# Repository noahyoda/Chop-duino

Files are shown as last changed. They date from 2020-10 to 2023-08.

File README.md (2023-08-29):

# Chopduino

### Author(s): Noah Jaussi

STEM Capstone Project

### Abstract

The goal of this experiment is to design and build a device that can electronically control a pair of chopsticks with the right precision to be used by people, who have disabilities that prevents them from using chopsticks to feed themselves. This project went through several design iterations before the final design was decided upon. Using an arduino pro micro, 18650 battery cell, an analog switch, the arduino IDE, windows 3d builder, a soldering iron, and a 3d printer to manufacture and assemble the necessary components, this project was able to make use of Science, Technology, Engineering, and Math (STEM). The process of designing and troubleshooting would not have been possible if it wasn’t for the research done beforehand, especially in the field of arduino wiring and programming. The process of prototyping this device followed the process of  testing all of the electronics on a breadboard, soldering them together, programming the arduino to function properly, modeling the base structure, 3d printing the necessary components, and assembling the frame and the electronics into their final form to be trialed for functionality improvements. There were many challenges encountered that arose in each technical division of this project and it continues to have room for improvement in future designs, should this project be continued, in the areas of size, comfort, sound deadening, and aesthetic appeal however it did fulfill all of the engineering goals it was originally set out to accomplish.

### Introduction

 In order to create the object of this project there are several techniques, programs, and skills that need to be acquired to ensure success. First it is necessary to understand the hardware required and the essential properties/interactive capabilities of said hardware for optimal performance. This includes the physical parameters for the servo, connections of the mechanical switch and button, and the pinout/specs for the microcontroller. These devices will be required to interact with the program set to be installed on the microcontroller so as to perform the functions it is intended to complete. In order to accomplish isolated and untethered operation, a rechargeable 18650 battery cell will be included, as it’s nature allows both high current power draw for the servo and consistent power output for the raw inputs on the microcontroller. Aside from the electronics, a housing will need to be constructed from 3d printed plastic which has to be confirmed to be safe for human contact. This is especially vital in this project, due to the nature and proximity the 3d printed plastics will be to objects being consumed by users. The plastic will need to be strong enough to endure the nature of its intended use while also being flexible enough to provide smooth movements for precise control.

 The most essential part of this project is the microcontroller, which will require proper implementation of its pinout abilities and programming. The Arduino Pro Micro includes 14 digital in/out (also I/O) leads and 4 analog I/O leads. This project will require one digital lead to communicate with the servo and one analog lead to interpret the incoming information from the user. The user will interact with the project via a button switch on the side. After properly connecting the switch and servo the Arduino, the micro controller chip will need to be programmed using an Integrated Development Environment (IDE), such as the one provided at arduino.cc for the specific ATMega chip on the Arduino Pro Micro. There are many options for IDE’s, however, the arduino.cc IDE was chosen for its preferential level of documentation and development status. This IDE also includes firmware that is needed to ensure that the ATMega chip in the Arduino is programmed without any issues and will utilize proper functionality. Detailed information and more on these subjects were found at Arduino.cc and the Make: Getting Started with Arduino book (Source 1).

 Programming this Arduino microcontroller will require not only hardware documentation but an understanding of simple C++ programming knowledge, as is dictated by the IDE. This is necessary as the complex nature of the task, in terms of electronics, is not something that can be easily performed without a microcontroller. The arduino will need to communicate user input from the switch to the servo in a way that translates on/off into a degree or number of rotations that the servo needs (Source 3). These translations of electrical signals will be interpreted and sent out through the program given to the arduino microcontroller.

 In order to power the Arduino and its necessary accessories, an 18650 lithium ion battery cell will be included with a voltage and current regulator to ensure proper power distribution is delivered to the electronics. This amplification and control will occur on the arduino board. It will also limit the amperage in order to protect the sensitive electronics from the high power draw of the servo motor. The 18650 battery cells are lithium ion, which means that the battery in this project will need to have overcharge/discharge protection circuits. This is necessary, not only to ensure battery life, but also to prevent the battery from becoming a fire hazard. According to previous research and the properties of power distribution in arduinos, these concerns will not manifest should the project be assembled exactly according to its design guidelines (Source 2).

 To make the prototyping and development of this project faster, a 3d printer will be used to make the frame and housing for the electronics as well as other necessary items. Having plastics that are toxic to humans and not rigid enough to support the required components are important design concerns to be considered for this project. Fortunately, these concerns has been tested before and it has been found that consumer grade Acrylonitrile butadiene styrene (ABS) and Thermoplastic Polyurethane (TPU) plastic filament are both not toxic to humans (unless burned and fumes are inhaled, see source 5) and provide the mixture of strength and flexibility required for this projects success (source 4). There are many other plastics that could be used but considering this project’s proximity to food that will be consumed, ABS and TPU plastics were decided upon as the final developing material for this project.

### Materials and Procedures

Materials:

-   Computer to run Windows 3d builder    
-   3d printer (creality ender 3)
-   ABS + TPU 3d printer filament
-   18650 battery
-   Arduino pro micro
-   Analog switch    
-   Breadboard    
-   Wire clips    
-   Chopsticks    
-   Soldering iron + solder   
-   Wires    
-   Small tension spring
-   9g servo    

### Procedure:

1.  Prototype electronics circuit on breadboard
2.  Revise until all connections are functional
3.  Design code for arduino
4.  Upload and test code in arduino
5.  Revise code until proper functionality
6.  Open 3d builder and design first 3d printable prototype
7.  Save 3d model in cura printing software
8.  Upload model to 3d printer
9.  Solder electronics together while model is 3d printing
10.  Assemble 3d model and observe potential changes
11.  Return to 3d builder to add changes to the 3d model
12.  Begin print of revised model
13.  Repeat assemble, observation, edit, and 3d print until fully functional design is achieved
  
### Data Analysis

Figure A: Prototype v.1





Figure B: Prototype v.1.2





FIgure C: Prototype v.2





Electronics v.1



Electronics Diagram



Engineering Challenges

Observations

1
-   Initially the electronics were assembled and tested which proved trials as the analog pin  for the switch was giving off unusual pulses making the servo uncontrollable. This was fixed with an analogWrite(_,0); statement to reset the analog signal on pin A0 to zero after every run of the program.
    
2

-   While testing the electronics the first servo broke and would spin out of control so several more servos were tested until a 180* servo worked with full control.

3
-   When assembling the 3d printed frame the plastic had to be welded together using a soldering iron which was a challenge and required the use of multiple prints to get successful and strong bonds.
    
4
-   The servo placement on the printed frame required multiple trials before it could provide the proper tension on the spring to pull the pivoting chopstick into place and push it back when finished with its cycle. To solve this the servo was placed on the bottom of the overall device.
    
5
-   The final challenge before the working product was chopstick alignment. The moving chopstick had the challenge of shifting the still chopstick far enough out of place that it proved not functional. This was resolved by welding a plastic brace over the still chopstick.
    
6
-   There was difficulty getting an ir distance sensor to ship to Hawaii so a model function change was altered to use a button for activation of the software devices in place of the distance sensor as originally planned.

### Conclusion

This project is based on the idea that STEM can create a device that provides functionality to those in need of assistive eating devices. The result of this idea was an electronically controlled, self-contained device that can close, hold closed, and open a pair of chopsticks under the control of a single button. This device encountered many challenges as prototypes were developed that had to be overcome in many unique ways that incorporated all fields of STEM.

  In chronological order of development, the first engineering challenge encountered was found in the connections between the switch/button and servo to the ATMega chip controlling the Arduino pro micro. The pins were either being shared with other logic data lines on the Arduino or there was interference that would cause the electrical values of the pins to vary from 0 to 1000 (state of all off to all on). This complication would cause the button to not be recognized while being pushed and the servo to twitch and not respond at times. The troubleshooting process for this problem required analysis into the electrical engineering of the Arduino pro micro to find the problem and then was resolved in the technological field through extra lines to the code. By adding analog write functions to reset the button pin value every time the program is run, the Arduino verified the switch position value. This switch problem was resolved by using the digital write function. The servo was able to reassign the pin value to the servo rotational status in a way to keep it in the proper orientation and clear the interference that the connection was experiencing. During the process of troubleshooting these issues, the first servo burnt out and had to be replaced. The next issue was found in the code, which would not reset the servo position at times and not react to user input through the button on other occasions. This was found, in the troubleshooting process, to be the fault of using an if-else statement to run the servo. To remedy this issue, more technical aspects were applied through a double “if” statement, which was used to run individual loops for the function of opening and closing the servo direction. Following this, the 3d model was designed and printed for the housing of the project, which went through several designs before being functional. The first design had an error in which the gear sockets were printed too far apart to prevent the gears from interacting. This was fixed by bringing the gears 5mm closer to each other. After fixing that, it was found that the design did not have enough room for the electronics needed and more importantly could not provide the servo with a position to get enough leverage to move the chopsticks into open and closed positions. Eventually, the model was scrapped and a new model was designed based on the flexibility of the 3d printed plastic rather than a gear system that solved the electronic housing and servo positioning issues but required more plastic welding to be assembled.

  Having built a functioning project that completes the engineering requirements set at the beginning of this project, there are several things that could be done differently or better upon repeating this project. The project would greatly benefit from precise measurements with better software to require less post-processing in the assembly. Additionally, adding rails to guide the chopsticks and downsizing the flexible joint for the chopsticks would improve performance. More time could be spent making a better grip for the model would improve the comfort of the device. As far as electronics are concerned, a custom circuit board with power and grounding rails, rather than the current clips, would help with downsizing the project. In the future a single ATTiny chip could also be used to decrease size and power consumption alongside the custom PCB. The solder joints could be improved with more flux in the joints that could increase their potential longevity and efficiency. Alongside that, adding a circuit to reset the servo position before cutting the power, after hitting the power switch, would reduce manual maintenance. Silicon coating on the electronics would make them waterproof to alleviate the concern when using this device for eating near liquids. The code for this project isn’t as efficient as it could be and could use cleaning. This could also be solved by using a different chip, such as the ATTiny, which would not require a solution to fix interference. The code could also use some changes to make the servo quieter. The battery would benefit from the use of a step-up circuit to provide power at a higher voltage to the servo and decrease the motor noise.

This experiment provides a solution for individuals with disabilities, who struggle to feed themselves without assistance, by automating processes that are not within their capabilities and necessary to be independent. This device automates the coordination and strength required to precisely close and hold onto an object using chopsticks to feed themselves. By simplifying these actions to the control of a button press, people are able to focus on carrying food to their mouth without requiring the assistance that would be necessary to perform this action otherwise.

## References

Source 1

Banzi, M., & Shiloh, M. (2014). Make: Getting Started with Arduino. Maker Media, Inc. 

Source 2

Ecker, M., Nieto, N., Käbitz, S., Schmalstieg, J., Blanke, H., Warnecke, A., & Sauer, D. U. (2013, October 11). Calendar and cycle life study of Li(NiMnCo)O2-based 18650 lithium-ion batteries. Retrieved from https://www.sciencedirect.com/science/article/abs/pii/S0378775313016510.

Source 3

Minns, P. D. (2013). C programming for the Pc the Mac and the Arduino microcontroller system. Bloomington, IN: AuthorHouse.

Source 4

SajTom Light Future. (n.d.). Is 3D printing safe? Analysis of the thermal treatment of thermoplastics: ABS, PLA, PET, and nylon. Retrieved from https://www.tandfonline.com/doi/abs/10.1080/15459624.2017.1285489.

Source 5

nnn946@gmail.com. “TPU Filament 3D Printing Material – The Complete Guide (Mar. 2020).” AllThat3D, AllThat3D, 25 Oct. 2019, www.allthat3d.com/tpu-filament/. 

Source 6

Warren, J.-D., Adams, J., & Molle, H. (1970, January 1). Arduino for Robotics. Retrieved from [https://link.springer.com/chapter/10.1007/978-1-4302-3184-4_2](https://link.springer.com/chapter/10.1007/978-1-4302-3184-4_2).

Source 7

My Continuous Rotation Servo Won't Stop Spinning?, 27 Feb. 2015, forum.arduino.cc/index.php?topic=304146.0.

Source 8

“How to Make My Servo Stop Twitching.” How to Make a Servo Stop Twitching, 26 June 2018, forum.arduino.cc/index.php?topic=555150.0.

Source 9

“Language Reference.” Arduino Reference, www.arduino.cc/reference/en/.

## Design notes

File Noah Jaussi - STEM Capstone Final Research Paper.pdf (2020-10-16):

# Chopduino

## Noah Jaussi - Kahuku High School

## STEM Capstone Project

# Abstract

The goal of this experiment is to design and build a device that can electronically control a pair of chopsticks with the right precision to be used by people, who have disabilities that prevents them from using chopsticks to feed themselves. This project went through several design iterations before the final design was decided upon. Using an arduino pro micro, 18650 battery cell, an analog switch, the arduino IDE, windows 3d builder, a soldering iron, and a 3d printer to manufacture and assemble the necessary components, this project was able to make use of Science, Technology, Engineering, and Math (STEM). The process of designing and troubleshooting would not have been possible if it wasn’t for the research done beforehand, especially in the field of arduino wiring and programming. The process of prototyping this device followed the process of testing all of the electronics on a breadboard, soldering them together, programming the arduino to function properly, modeling the base structure, 3d printing the necessary components, and assembling the frame and the electronics into their final form to be trialed for functionality improvements. There were many challenges encountered that arose in each technical division of this project and it continues to have room for improvement in future designs, should this project be continued, in the areas of size, comfort, sound deadening, and aesthetic appeal however it did fulfill all of the engineering goals it was originally set out to accomplish.

# Introduction

In order to create the object of this project there are several techniques, programs, and skills that need to be acquired to ensure success. First it is necessary to understand the hardware required and the essential properties/interactive capabilities of said hardware for optimal performance. This includes the physical parameters for the servo, connections of the mechanical switch and button, and the pinout/specs for the microcontroller. These devices will be required to interact with the program set to be installed on the microcontroller so as to perform the functions it is intended to complete. In order to accomplish isolated and untethered operation, a rechargeable 18650 battery cell will be included, as it’s nature allows both high current power draw for the servo and consistent power output for the raw inputs on the microcontroller. Aside from the electronics, a housing will need to be constructed from 3d printed plastic which has to be confirmed to be safe for human contact. This is especially vital in this project, due to the nature and proximity the 3d printed plastics will be to objects being consumed by users. The plastic will need to be strong enough to endure the nature of its intended use while also being flexible enough to provide smooth movements for precise control. The most essential part of this project is the microcontroller, which will require proper implementation of its pinout abilities and programming. The Arduino Pro Micro includes 14 digital in/out (also I/O) leads and 4 analog I/O leads. This project will require one digital lead to communicate with the servo and one analog lead to interpret the incoming information from the user. The user will interact with the project via a button switch on the side. After properly connecting the switch and servo the Arduino, the micro controller chip will need to be programmed using an Integrated Development Environment (IDE), such as the one provided at arduino.cc for the specific ATMega chip on the Arduino Pro Micro. There are many options for IDE’s, however, the arduino.cc IDE was chosen for its preferential level of documentation and development status. This IDE also includes firmware that is needed to ensure that the ATMega chip in the Arduino is programmed without any issues and will utilize proper functionality. Detailed information and more on these subjects were found at Arduino.cc and the Make: Getting Started with Arduino book (Source 1).
Programming this Arduino microcontroller will require not only hardware documentation but an understanding of simple C++ programming knowledge, as is dictated by the IDE. This is necessary as the complex nature of the task, in terms of electronics, is not something that can be easily performed without a microcontroller. The arduino will need to communicate user input from the switch to the servo in a way that translates on/off into a degree or number of rotations that the servo needs (Source 3). These translations of electrical signals will be interpreted and sent out through the program given to the arduino microcontroller.
In order to power the Arduino and its necessary accessories, an 18650 lithium ion battery cell will be included with a voltage and current regulator to ensure proper power distribution is delivered to the electronics. This amplification and control will occur on the arduino board. It will also limit the amperage in order to protect the sensitive electronics from the high power draw of the servo motor. The 18650 battery cells are lithium ion, which means that the battery in this project will need to have overcharge/discharge protection circuits. This is necessary, not only to ensure battery life, but also to prevent the battery from becoming a fire hazard. According to previous research and the properties of power distribution in arduinos, these concerns will not manifest should the project be assembled exactly according to its design guidelines (Source 2). To make the prototyping and development of this project faster, a 3d printer will be used to make the frame and housing for the electronics as well as other necessary items. Having plastics that are toxic to humans and not rigid enough to support the required components are important design concerns to be considered for this project. Fortunately, these concerns has been tested before and it has been found that consumer grade Acrylonitrile butadiene styrene (ABS) and Thermoplastic Polyurethane (TPU) plastic filament are both not toxic to humans (unless burned and fumes are inhaled, see source 5) and provide the mixture of strength and flexibility required for this projects success (source 4). There are many other plastics that could be used but considering this project’s proximity to food that will be consumed, ABS and TPU plastics were decided upon as the final developing material for this project.

# Materials and Procedures

Materials:
- Computer to run Windows 3d builder
- 3d printer (creality ender 3)
- ABS + TPU 3d printer filament

- 18650 battery
- Arduino pro micro
- Analog switch
- Breadboard
- Wire clips
- Chopsticks
- Soldering iron + solder
- Wires
- Small tension spring
- 9g servo

Procedure:
1. Prototype electronics circuit on breadboard
2. Revise until all connections are functional
3. Design code for arduino
4. Upload and test code in arduino
5. Revise code until proper functionality
6. Open 3d builder and design first 3d printable prototype
7. Save 3d model in cura printing software
8. Upload model to 3d printer
9. Solder electronics together while model is 3d printing 10.Assemble 3d model and observe potential changes
11.Return to 3d builder to add changes to the 3d model
12.Begin print of revised model
13.Repeat assemble, observation, edit, and 3d print until fully functional design is achieved

# Data Analysis

Figure A: Prototype v.1

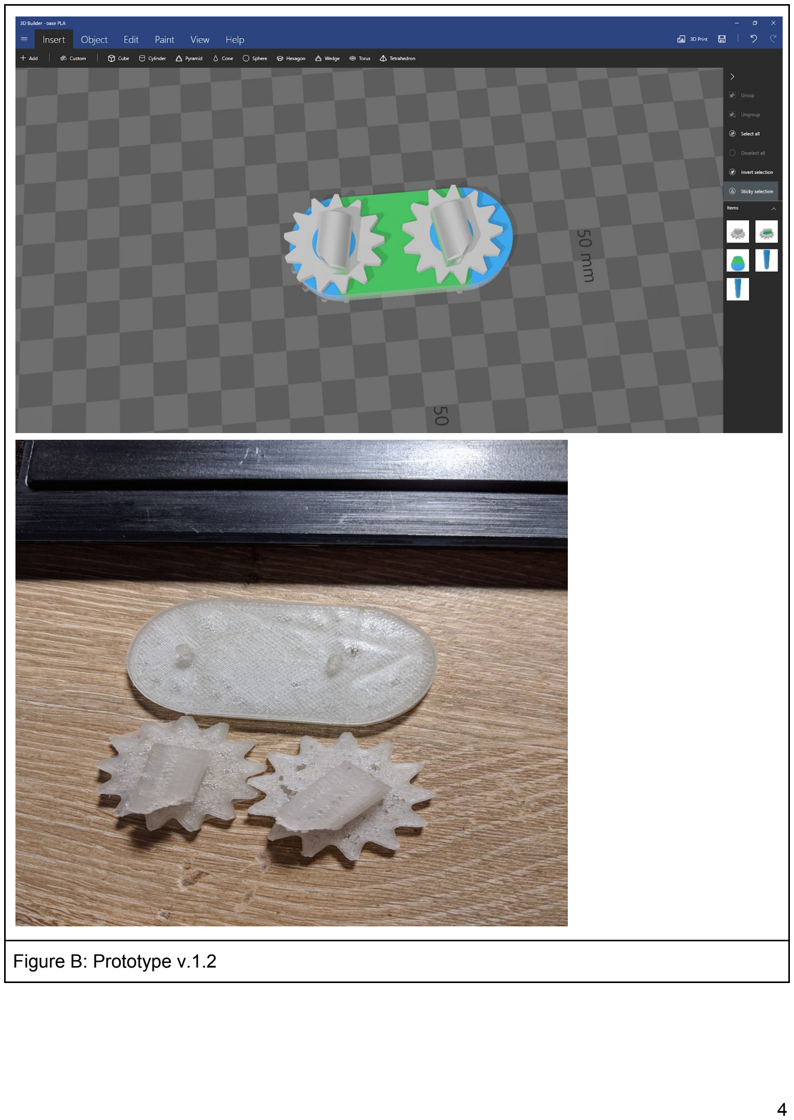
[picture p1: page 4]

Figure B: Prototype v.1.2

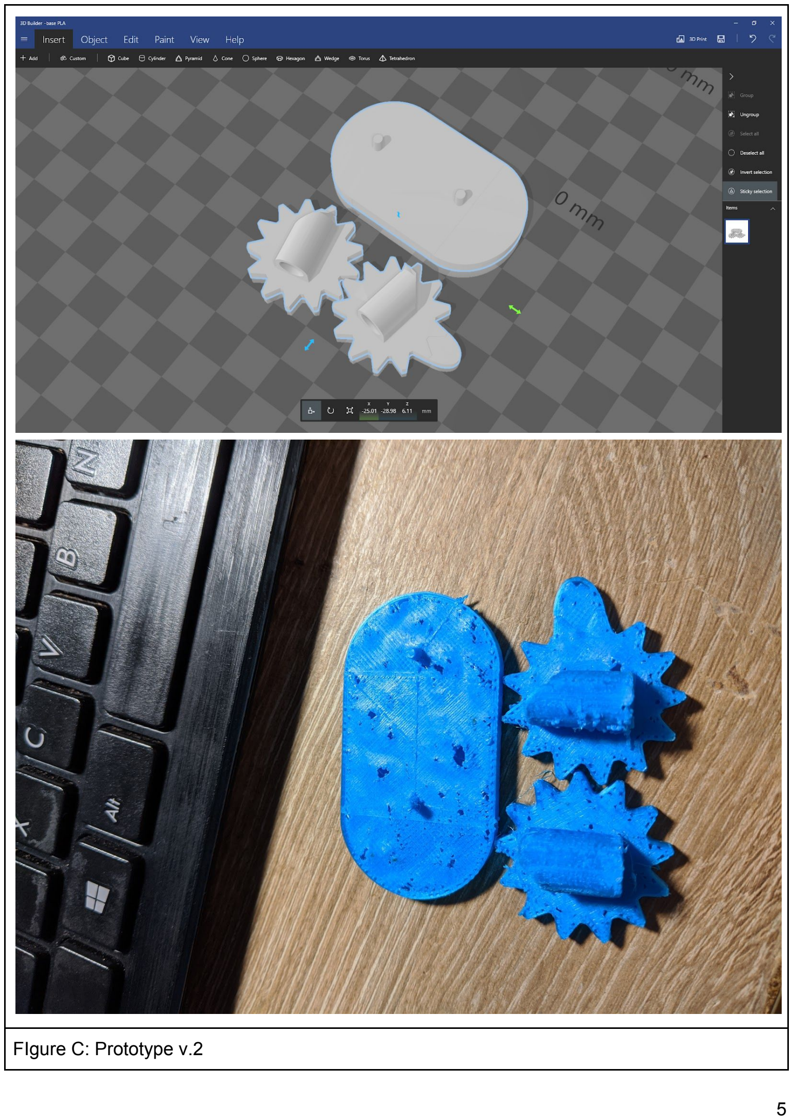
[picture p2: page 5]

FIg

u

r

e

C: P

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
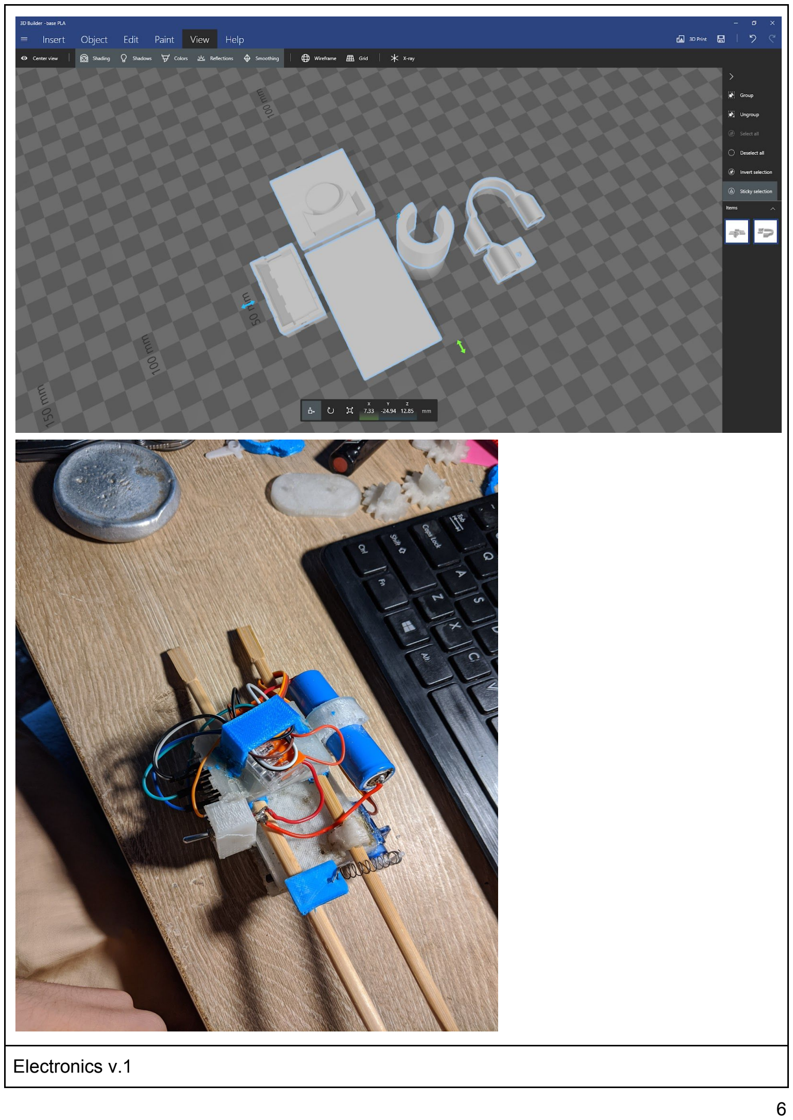
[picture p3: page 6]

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
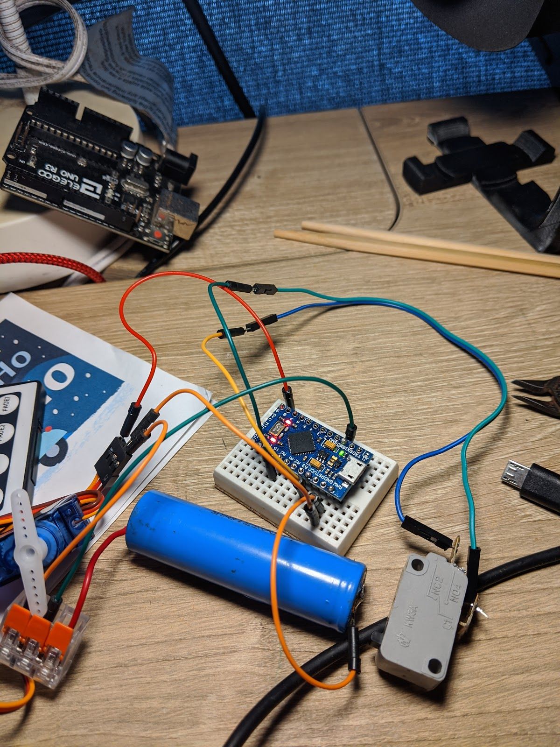
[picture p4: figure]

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
rv; int switchA

=

A

0; int val = 0; void setup() { // put setup code

h

e

r

e
s

e

rv.a

t

t

a

c

h

(

9

); serv.write(0); delay(100); val = analogRe

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
); //pinMode(15, INPUT); }void loop() { // put your main code here

if(val > 1000){
//serv.attach(9);
while(val > 1000){
serv.write(90);
}
} else {
//serv.attach(9);
serv.write(0);
//serv.detach();

delay(300);
}
}

Code v.2

#include <Servo.h>

Servo myservo; // create servo object to control a servo

int pos = 0; // variable to store the servo position int button = 4; // The button will be on Pin 4
int val = 0;
int switchA = A0;

void setup(){
myservo.attach(9); // attaches the servo on pin 9 to the servo object pinMode(pos, OUTPUT);
pinMode(button, INPUT);
digitalWrite (button, LOW);
Serial.begin(9600);
}

void loop(){
Serial.println(val);
val = analogRead(switchA);
if (val > 1000)
for(pos = 0; pos < 90; pos += 90){ // goes from 0 degrees to 90 degrees
myservo.write(pos); | // tell servo to go to position in variable 'pos'
delay(30); | // waits for the servo to reach the position
}
if (val < 1000)
for(pos = 90; pos>=90; pos-=90){ // goes from 90 degrees to 0 degrees
myservo.write(pos); | // tell servo to go to position in variable 'pos'
delay(100); | // waits for the servo to reach the position
analogWrite(val, 0);

}
}

Electronics Diagram

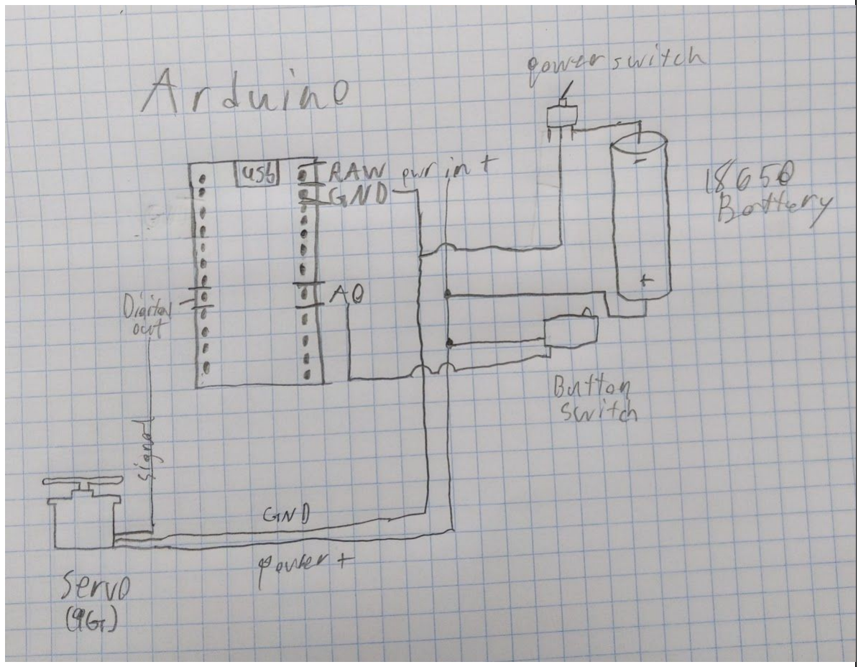
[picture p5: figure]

Engineerin g Challenges | Observations
1 | ● Initially the electronics were assembled and tested which proved trials as the analog pin for the switch was giving off unusual pulses making the servo uncontrollable. This was fixed with an analogWrite(_,0); statement to reset the analog signal on pin A0 to zero after every run of the program.
2 | ● While testing the electronics the first servo broke and would spin out of

| control so several more servos were tested until a 180* servo worked with full control.
3 | ● When assembling the 3d printed frame the plastic had to be welded together using a soldering iron which was a challenge and required the use of multiple prints to get successful and strong bonds.
4 | ● The servo placement on the printed frame required multiple trials before it could provide the proper tension on the spring to pull the pivoting chopstick into place and push it back when finished with its cycle. To solve this the servo was placed on the bottom of the overall device.
5 | ● The final challenge before the working product was chopstick alignment. The moving chopstick had the challenge of shifting the still chopstick far enough out of place that it proved not functional. This was resolved by welding a plastic brace over the still chopstick.
6 | ● There was difficulty getting an ir distance sensor to ship to Hawaii so a model function change was altered to use a button for activation of the software devices in place of the distance sensor as originally planned.

# Conclusion

This project is based on the idea that STEM can create a device that provides functionality to those in need of assistive eating devices. The result of this idea was an electronically controlled, self-contained device that can close, hold closed, and open a pair of chopsticks under the control of a single button. This device encountered many challenges as prototypes were developed that had to be overcome in many unique ways that incorporated all fields of STEM.
In chronological order of development, the first engineering challenge encountered was found in the connections between the switch/button and servo to the ATMega chip controlling the Arduino pro micro. The pins were either being shared with other logic data lines on the Arduino or there was interference that would cause the electrical values of the pins to vary from 0 to 1000 (state of all off to all on). This complication would cause the button to not be recognized while being pushed and the servo to twitch and not respond at times. The troubleshooting process for this problem required analysis into the electrical engineering of the Arduino pro micro to find the problem and then was resolved in the technological field through extra lines to the code. By adding analog write functions to reset the button pin value every time the program is run, the Arduino verified the switch position value. This switch problem was resolved by using the digital write function. The servo was able to reassign the pin value to the servo rotational status in a way to keep it in the proper orientation and clear the interference that the connection was experiencing. During the process of troubleshooting these issues, the first servo burnt out and had to be replaced. The next issue was found in the code, which would not reset the servo position at times and not react to user input through the button on other occasions. This was found, in the troubleshooting process, to be the fault of using an if-else statement to run the servo. To remedy this issue, more technical aspects were applied through a double “if” statement, which was used to run individual loops for the function of opening and closing the servo direction. Following this, the 3d model was designed and printed for the housing of the project, which went through several designs before being functional. The first design had an error in which the gear sockets were printed too far apart to prevent the gears from interacting. This was fixed by bringing the gears 5mm closer to each other. After fixing that, it was found that the design did not have enough room for the electronics needed and more importantly could not provide the servo with a position to get enough leverage to move the chopsticks into open and closed positions. Eventually, the model was scrapped and a new model was designed based on the flexibility of the 3d printed plastic rather than a gear system that solved the electronic housing and servo positioning issues but required more plastic welding to be assembled.
Having built a functioning project that completes the engineering requirements set at the beginning of this project, there are several things that could be done differently or better upon repeating this project. The project would greatly benefit from precise measurements with better software to require less post-processing in the assembly. Additionally, adding rails to guide the chopsticks and downsizing the flexible joint for the chopsticks would improve performance. More time could be spent making a better grip for the model would improve the comfort of the device. As far as electronics are concerned, a custom circuit board with power and grounding rails, rather than the current clips, would help with downsizing the project. In the future a single ATTiny chip could also be used to decrease size and power consumption alongside the custom PCB. The solder joints could be improved with more flux in the joints that could increase their potential longevity and efficiency. Alongside that, adding a circuit to reset the servo position before cutting the power, after hitting the power switch, would reduce manual maintenance. Silicon coating on the electronics would make them waterproof to alleviate the concern when using this device for eating near liquids. The code for this project isn’t as efficient as it could be and could use cleaning. This could also be solved by using a different chip, such as the ATTiny, which would not require a solution to fix interference. The code could also use some changes to make the servo quieter. The battery would benefit from the use of a step-up circuit to provide power at a higher voltage to the servo and decrease the motor noise.
This experiment provides a solution for individuals with disabilities, who struggle to feed themselves without assistance, by automating processes that are not within their capabilities and necessary to be independent. This device automates the coordination and strength required to precisely close and hold onto an object using chopsticks to feed themselves. By simplifying these actions to the control of a button press, people are able to focus on carrying food to their mouth without requiring the assistance that would be necessary to perform this action otherwise.

# References

Source 1
Banzi, M., & Shiloh, M. (2014). Make: Getting Started with Arduino. Maker Media, Inc. Source 2
Ecker, M., Nieto, N., Käbitz, S., Schmalstieg, J., Blanke, H., Warnecke, A., & Sauer, D. U. (2013, October 11). Calendar and cycle life study of Li(NiMnCo)O2-based 18650 lithium-ion batteries. Retrieved from https://www.sciencedirect.com/science/article/abs/pii/S0378775313016510.
Source 3
Minns, P. D. (2013). C programming for the Pc the Mac and the Arduino microcontroller system. Bloomington, IN: AuthorHouse.
Source 4
SajTom Light Future. (n.d.). Is 3D printing safe? Analysis of the thermal treatment of thermoplastics: ABS, PLA, PET, and nylon. Retrieved from https://www.tandfonline.com/doi/abs/10.1080/15459624.2017.1285489.
Source 5
nnn946@gmail.com. “TPU Filament 3D Printing Material – The Complete Guide (Mar. 2020).” AllThat3D, AllThat3D, 25 Oct. 2019, www.allthat3d.com/tpu-filament/.
Source 6
Warren, J.-D., Adams, J., & Molle, H. (1970, January 1). Arduino for Robotics. Retrieved from https://link.springer.com/chapter/10.1007/978-1-4302-3184-4_2.
Source 7
My Continuous Rotation Servo Won't Stop Spinning?, 27 Feb. 2015, forum.arduino.cc/index.php?topic=304146.0.
Source 8
“How to Make My Servo Stop Twitching.” How to Make a Servo Stop Twitching, 26 June 2018, forum.arduino.cc/index.php?topic=555150.0.
Source 9
“Language Reference.” Arduino Reference, www.arduino.cc/reference/en/.

# Grading Rubric (DO NOT EDIT)

Grade

Teacher Rubric Settings: t10060tftc jrasmussen _

Rubric Categories | Exemplary | Meets Proficiency | Approaching Proficiency | Developing Proficiency
Content Understanding | Report reflects an overall accurate and thorough understanding of all included S, T, E, and M content and concepts. | Report reflects an overall accurate understanding of most included S, T, E, and M content and concepts. | Report reflects a limited understanding of all included S, T, E, and M content and concepts. | Report reflects a misunderstandin g or lack of included S, T, E, and M content.
Introduction and | Clearly stated, introduces the topic of the | Clearly stated, introduces the topic of the | In the introduction, the topic of the | The topic of the paper and research

Background paper and the main points to be discussed. Explains background information, presents the research problem or questions with rationale.

paper. Provides
background
information and
presents the
research
problem or
questions.

paper and the
research
problem or
questions are
stated, but need
to be clarified or
refined.

problem or
questions are
unclear or not
stated.

Materials and
Procedures

Testable
hypotheses or
predictions are
clearly
articulated.
Research design
is appropriate to
the research
problem/questio
ns. Procedures
are described in
paragraph form,
outlined
sequentially,
and adequately
detailed.

Testable
hypotheses or
predictions are
stated.
Research design
is mostly
appropriate to
the research
problem/questio
ns. Procedures
are described in
paragraph form,
sequentially,
and detailed.

Hypotheses are
not testable or
incomplete.
Research design
needs
improvement to
address the
research
problem/questio
ns. Procedures
are not
described in
paragraph form
(e.g. bulleted
list) or not
sufficiently
detailed.

No hypotheses
or predictions
are stated.
Research design
is not
appropriate to
the research
problem/questio
ns. Procedures
are not
described or
inaccurate.
Results/Data | Data are presented clearly and cleanly, in tables or graphs as appropriate. Data are labeled and titled. | Data are presented clearly, in tables or graphs as appropriate. Data are labeled and titled. | Data are presented, but are unorganized and difficult to follow. | Data are not presented or inaccurate
Data Analysis | All calculations are shown and results are correct and labeled appropriately. | Most calculations are shown and results are correct and labeled appropriately. | Some calculations are shown and results are mostly labeled appropriately. | No calculations are shown OR results are inaccurate or mislabeled.

Conclusions

Conclusions
indicate whether
the hypothesis
was supported.
Claims about
interpretation of
the data are
supported by
evidence.
Explanations or
solutions
proposed are
based on
evidence.
Sources of
experimental
error or
limitations are
presented and
their possible
effects are
discussed.
Ways to reduce
error and
limitations are
proposed.

Conclusions
indicate whether
the hypothesis
was supported,
based on data.
Explanations or
solutions
proposed are
based on
evidence.
Sources of
experimental
error or
limitations are
presented.
Ways to reduce
error and
limitations are
proposed.

Conclusions
describe what
was learned in
the experiment,
but are not
based on data.
Experimental
errors may be
mentioned, but
are not
described.

No conclusions
are presented or
are not related
to the
investigation.

Organization

Purposeful
structure helps
reader follow
writer’s thinking.
Strong
lead—conclusio
n that provides
closure.
Thoughtful
transitions
clearly connect
ideas. Design
helps reader
process
ideas—main
ideas stand out.

Organization
makes it fairly
easy to follow
discussion.
Functional lead
and conclusion.
Helpful
transitions often
suggest
connections.
Overall design
works—writer
sometimes
dwells on trivia
or skims over
complex topics.

Reader can
follow
story/discussion
if attentive. Lead
formulaic or
misleading,
conclusion
formulaic or
abrupt.
Transitions
sometimes
missing or
mechanical.
Structure may
be formulaic or
confusing—paci
ng rushed or
sluggish.

Hard to follow,
even with effort.
Lead or
conclusion
missing,
formulaic, or
misleading.
Transitions
unclear, missing,
or not helpful in
linking ideas.
Significant
reorganization
needed—pacing
feels random
Writing | Strong control of | Reasonable | Limited control | Little or no

Conventions (Capitalization, spelling, word choice, grammar, spelling) | standard writing conventions, few errors | control of standard writing conventions, some editing necessary | of standard writing conventions, errors starting to impede readability | control of standard writing conventions, extensive errors impede readability
Sentence Fluency | Sentences well-built, strong and varied structure makes it easy to read. | Text flows, sentences somewhat varied, relatively easy to read. | Sentence structure awkward rather than fluid, reader must slow down. | Writing difficult to follow or read, many run-ons, fragments, choppy sentences, minimal variety in style, length.
Use of Sources | Abundant selection of supporting resource material is appropriate, current, and relevant. | Some supporting resource material, which is appropriate, current, and relevant. | Limited supporting resource material, which is partially appropriate, current, or relevant. | No supporting resource material or materials which are inappropriate, outdated, or irrelevant.
Citations and Works Cited | In-text citations and works cited are present, accurate, and correctly formatted for referenced research. | In-text citations are mostly present, accurate, and correctly formatted. | Limited in-text citations are present, partially accurate, or incorrectly formatted. | No in-text citations or works cited.
Manuscript Form (Typing, spacing, page numbers, headings) | No errors | Two or fewer errors | Four or fewer errors | Five or more errors
References | All 5 sources are cited properly throughout the entire report as needed and are also listed at the end. | 5 sources are cited in the references section and some are used properly throughout rest of the report. | 5 sources are cited in the references section. | Less than 5 sources are cited.

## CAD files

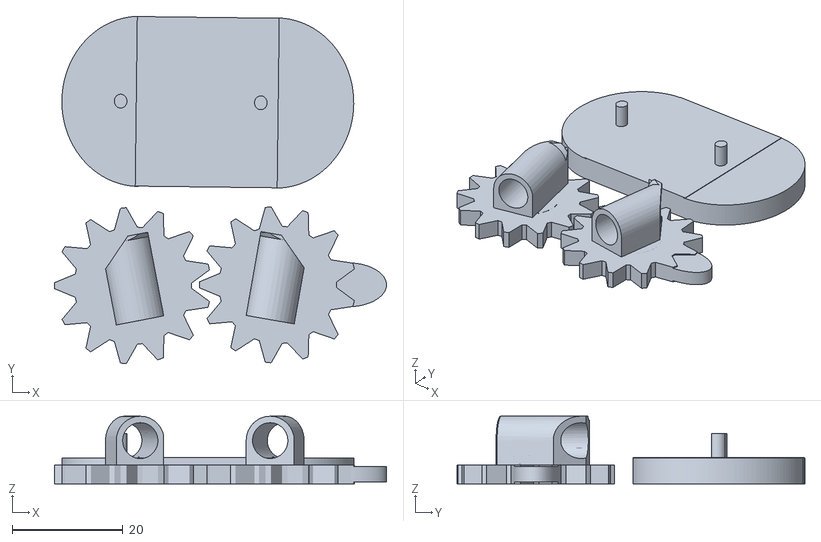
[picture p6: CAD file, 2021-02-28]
STEM Capstone stl versions/STEM Capstone v.2.stl
60.0 x 62.8 x 12.2

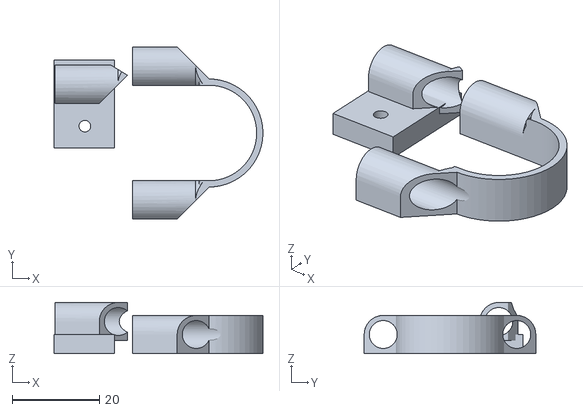
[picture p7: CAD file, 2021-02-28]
STEM Capstone stl versions/STEM Capstone v.3/bend TPU.stl
48.0 x 39.4 x 11.7

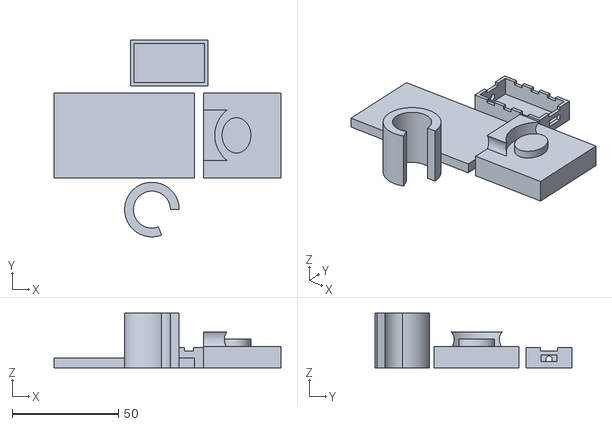
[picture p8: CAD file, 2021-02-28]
STEM Capstone stl versions/STEM Capstone v.3/base PLA.stl
106.8 x 92.6 x 25.7

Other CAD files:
STEM Capstone stl versions/STEM Capstone v.1.stl
